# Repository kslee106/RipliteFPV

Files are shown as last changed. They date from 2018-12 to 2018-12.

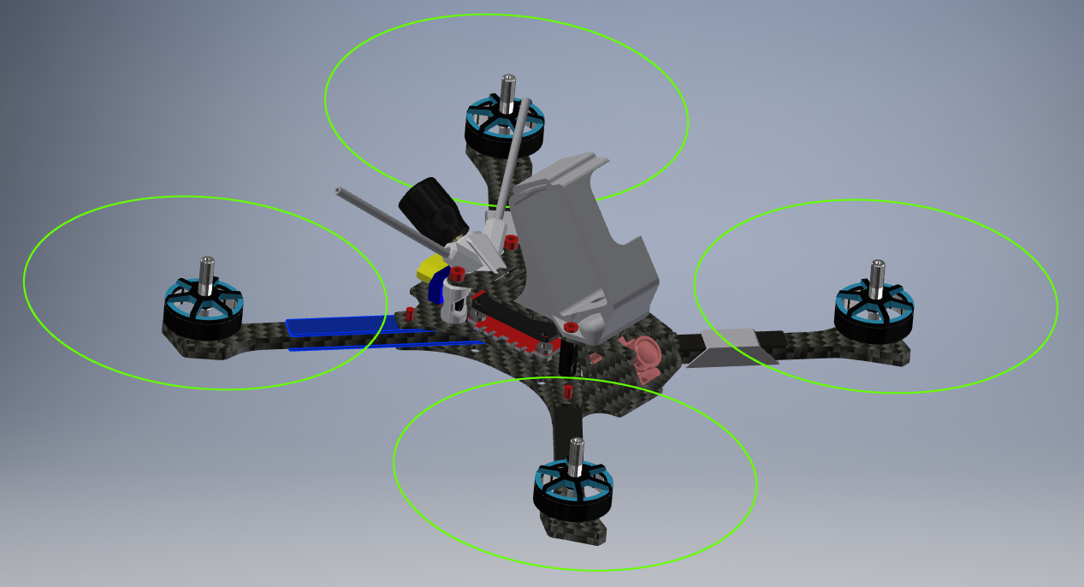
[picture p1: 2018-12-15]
12.15.2018 RL4.PNG

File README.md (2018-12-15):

# RipliteFPV

Riplite V4 FPV Frame

-True X Motor Spacing

-Micro Camera Mounting

-3D Printed Accessories

-5" Prop Max

Arm - 5mm thick

Body - 1.5mm thick.  Altering body thickness will change overall height and might make the camera plate unusable.  Holes in the body plate are for Rakon XT60 Mounts.  M3 holes with a 6mm long bolt (usually included with the mount).

Top - 1.5mm thick min.  The top plate has a center hole that was made for a sink nut (found on Armattan).  The sink nut is used for the GoPro mount.

Camera Plate - 2mm thick.  Recommend 006 size orings that go between the carbon and camera.  This is to help hold the camera in the set angle.  Slot in the camera plate is set at 45 degrees to help with setting the camera angle.  Requires 15mm standoffs for the normal build and 20mm standoffs if using the camera plate labeled "20mm".

Arm Spacer - 1mm thick

RaceWire - 1mm thick.  2oz copper minimum.

LEDs - 1mm thick.  1oz copper.  Requires WS2812b LEDs.  0604 1uF capacitor recommended but it works without it.  If you don't use the LEDs, you'll need 2 extra arm spacers to replace them.  Alternatively, if you want 4x LED boards, you won't need any arm spacers.

Antenna Mount - Printed with TPU.  Fits the SMA pigtail included with the TBS Unify VTX.  Held in with M3 6mm bolts.  Antenna tubes are the "Forever Tubes".  Will work with any 5mm dia standoffs (15mm tall).

RaceWire/LED Holders - Designed as keepers to secure the PCBs to the arm and prevent them from being ripped off.  Print in TPU.  They must be applied to the arm assembly before attaching the arm and wires to the frame.

GoPro Mount - GoPro H6/7 mount at 35 degrees.  Needs M3 2mm spacers to be inserted to help with TPU integrity.  The slots are for optional straps to keep the GoPro secure.  https://www.mouser.com/ProductDetail/761-M0501-3-AL?r=761-M0501-3-AL

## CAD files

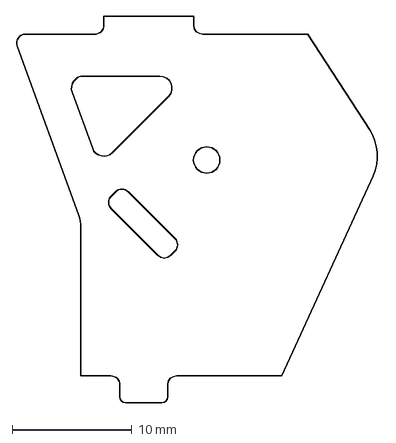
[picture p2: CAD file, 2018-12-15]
Cam Plate 20mm.dxf
30.3 x 32.3 mm

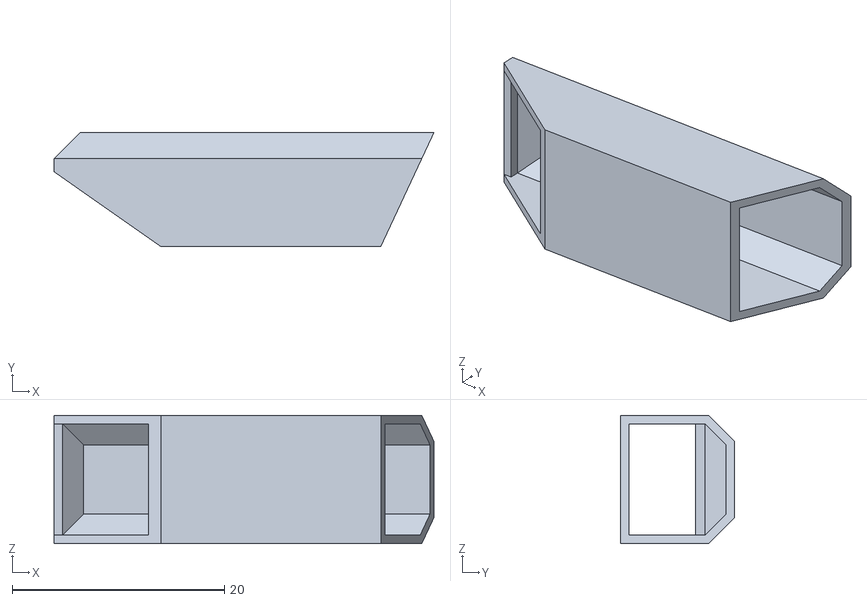
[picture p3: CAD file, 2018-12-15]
RW LED Holder.stl
35.8 x 10.7 x 12.1

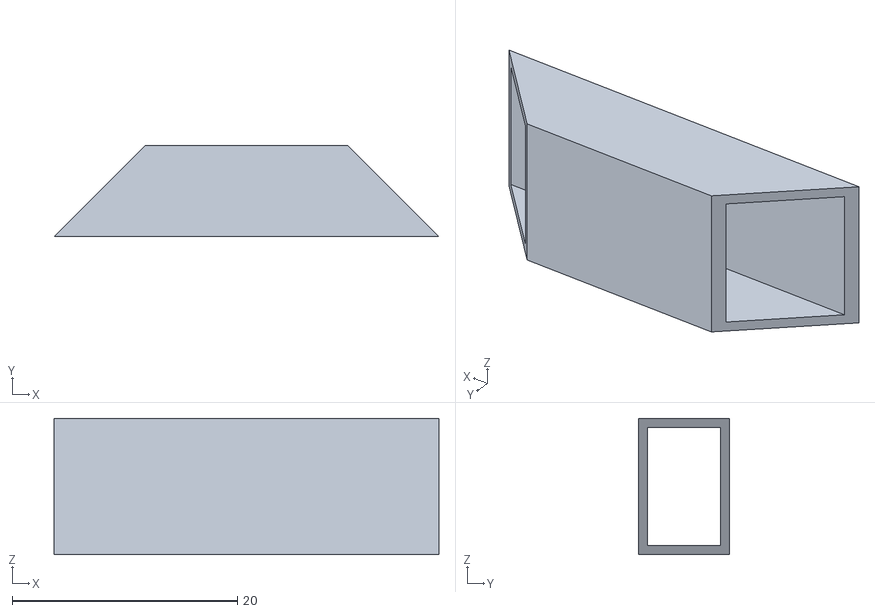
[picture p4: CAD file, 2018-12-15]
Front Arm RW Holder.stl
34.2 x 8.10 x 12.1

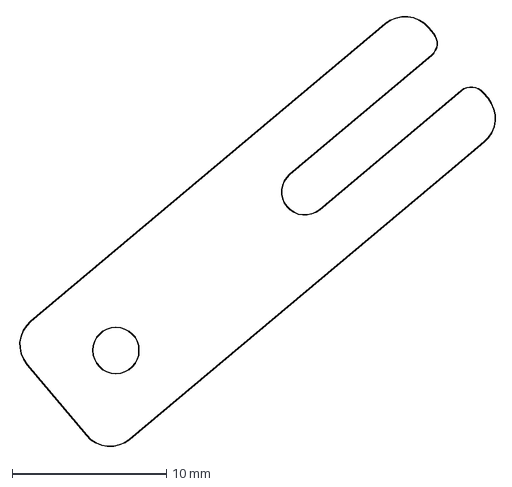
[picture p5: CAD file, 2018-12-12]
Spacer.dxf
31.1 x 28.0 mm

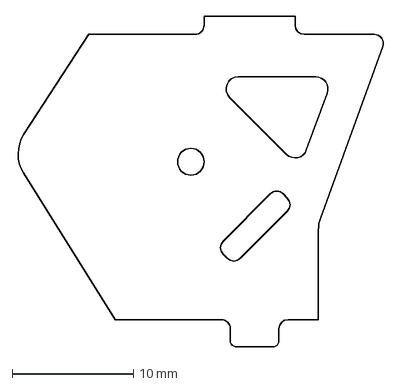
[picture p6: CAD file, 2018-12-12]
Cam Plate.dxf
30.3 x 27.3 mm

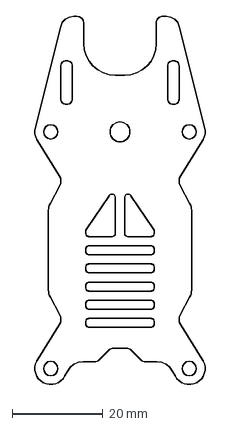
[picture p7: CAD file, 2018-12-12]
Top.dxf
38.5 x 81.5 mm

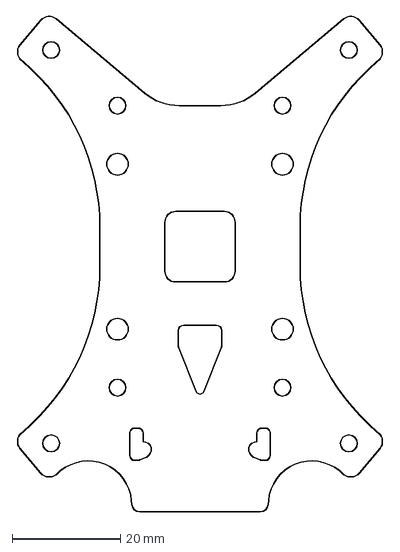
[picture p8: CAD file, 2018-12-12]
Body.dxf
67.9 x 91.6 mm

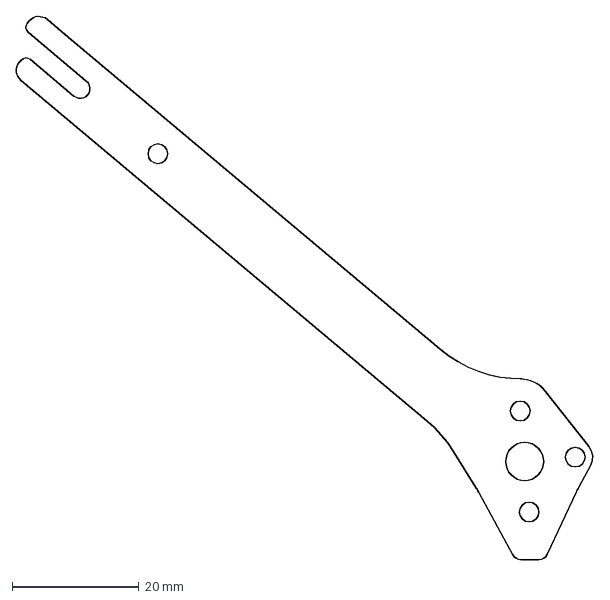
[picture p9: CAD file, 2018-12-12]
Arm.dxf
91.1 x 85.7 mm

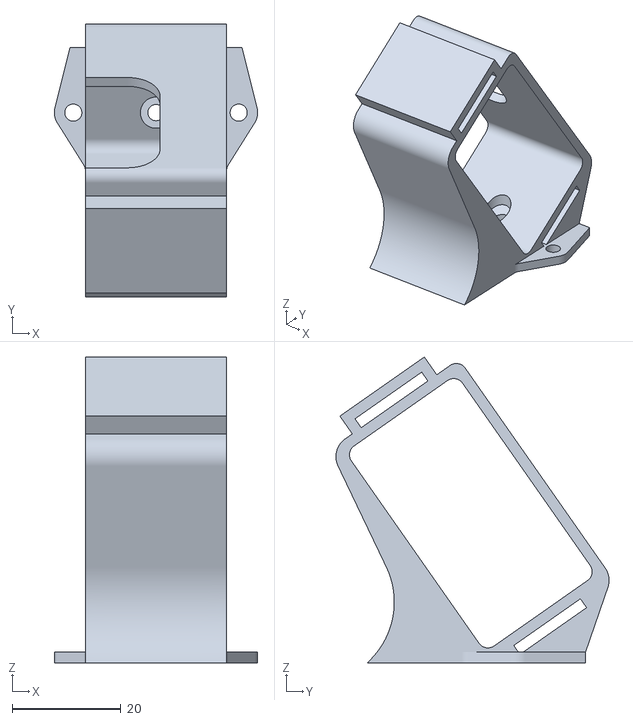
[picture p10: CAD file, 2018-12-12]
GoPro 35d.stl
37.5 x 50.3 x 56.4

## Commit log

2018-12-12 Riplite first upload
    [Arm.dxf, Body.dxf, Cam Plate.dxf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]
2018-12-15 Accessories upload
    LED PCBs requires 1mm thickness.
    RaceWire requires 1mm thickness and 2oz copper pour. Bottom must be insulated from carbon.
    [Front Arm RW Holder.stl, RW LED Holder.stl]
2018-12-15 Add files via upload
    Alternate camera plate for 20mm standoffs
    [Cam Plate 20mm.dxf]
